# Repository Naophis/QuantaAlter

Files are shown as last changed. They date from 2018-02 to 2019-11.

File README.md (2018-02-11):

# Quanta Alter

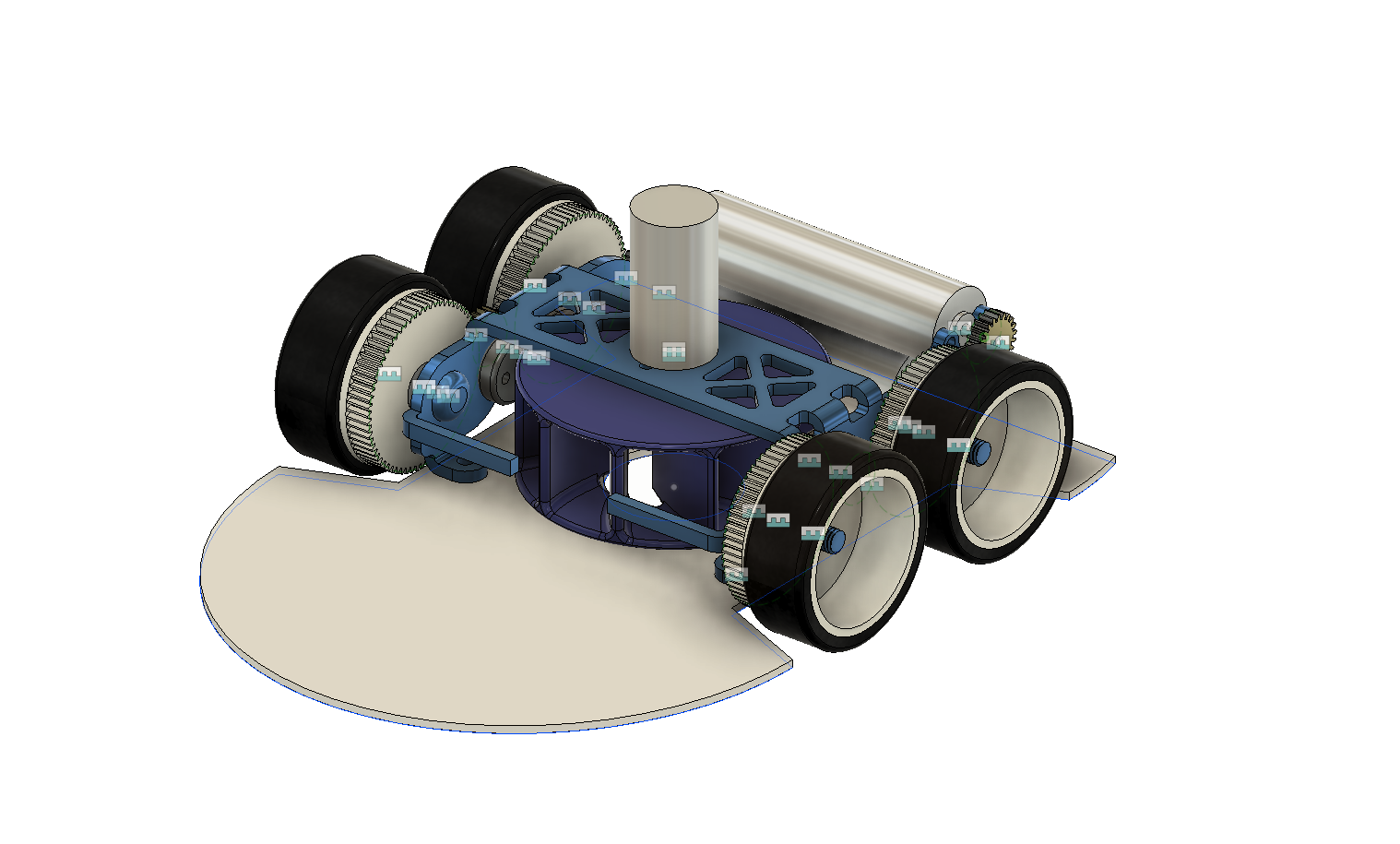
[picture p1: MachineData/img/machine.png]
QuantaAlter


## Getting started
```
git clone https://github.com/Naophis/QuantaAlter.git
```
## IDE
* e2studio

## Editor
* Visual Studio Code

## Writer
* Renesas Flash Programmer
  * Baudrate: 1228800 [bps]

## Machine Info
| | | |
|:---|---:|:---:|
|CPU|RX71M| - |
|Xtal|24M| - |
|Battery|3Cell| Lipo(4.2*3) |

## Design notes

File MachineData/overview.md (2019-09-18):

# ExiaAlter

| ||
|---|---|
|RobotName| ExiaAlter|
|Designer| Naoto Hiramatsu|
|Dimension | Width: 76.0mm, Length: 99.0mm, Height: 40.0mm|
|Weight| 110.0g |
|MCU|Renesas: R5F571MFCDFP|
|Mortor|Drive DCX-10L×2, Suction DCX-10S|
|Mortor Driver|TB6614FNG|
|Wall Sensor|SFH4550×5, ST-1KL3A×5|
|Gyroscope|ICM-20689|
|Battery|Lipo: Hyperion G5 200mah×3 3S(11.1V)|
|Gear ratio|21:67(M0.3)|
|TireSize|Diameter: 24.0m, Width: 8.5mm|
|Top/Turn Velocity|5.3m/s, 1.5~2.4m/s|

Features
* Suction is used both maze run and fast run.
* "ExiaConsole", which is Original Adjustment System, make adjustment time to be short. This console which is written in JavaSctipt can adjust almost all parameter on Web Browser and send/recieve data with UART. Robots recieve data from Console, write on Flash and use in running.

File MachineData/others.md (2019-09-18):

# Others

|	No	|	Name	|	Maker	|	Amount	|	Link	|	Remarks	|
|	---	|	---	|	---	|	---	|	---	|	---	|
|	1	| DCX10L(4.5orm) with easy10-encoder	| MAXON		|	2	|[URL](https://www.maxonjapan.co.jp/maxon/view/product/motor/dcmotor/DCX/DCX10/DCX10S01EBKL550)|	for driver	|
|	2	|	 DCX10S(3.orm)	|MAXON|	1	| [URL](https://www.maxonjapan.co.jp/maxon/view/product/motor/dcmotor/DCX/DCX10/DCX10S01EBKL550)|	for suction 	|
|	3	|	suction fun 	|	DMM3D print service	|	2	|| order made	|
|	4	|	G5 200mah	|	hyperion	|	3	| [URL](https://hyperion-world.com/en/charger-battery/batteries/hyperion-g5-lipo/g5-50cmax-1s-200mah-4-2v-max-lipo-w-phr-2p-connector)|	LiPo Battery	|
|	5	|	motor mount (frame)	|	NPS 	|	1	|| order made	|
|	6	|	zig	|	DMM3D 	|	2	|| order made	|
|	7	|	M0.3-67T-3mm-8mm(POM)	|	misumi 	|	4	|| Spur Gear	|
|	8	| M-0.3-21T-2mm-1.5mm(BRASS)	|	kkpmo 	|	4	|[URL](https://shop.kkpmo.com)| pinion	|

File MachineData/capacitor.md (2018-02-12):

# Capacitor

|	No	|	Value	|	Size	|	Amount	|	Link	|	Remarks	|
|	---	|	---	|	---	|	---	|	---	|	---	|
|	1	|	0.1u	|		|	10	|[URL](	https://www.digikey.jp/product-detail/ja/murata-electronics-north-america/GRM155R71C104JA88D/490-6327-1-ND/3845524	)|		|
|	2	|	180uF	|		|	2	|[URL](	https://www.sengoku.co.jp/mod/sgk_cart/detail.php?code=EEHD-4J4A	)|	motoro driver 	|
|	3	|	180uF	|		|	2	|[URL](	https://www.digikey.jp/product-detail/ja/wurth-electronics-inc/870235373002/732-6342-1-ND/5147893	)|	↑ or this	|
|	4	|	22u	|		|	1	|[URL](	https://www.digikey.jp/product-detail/ja/taiyo-yuden/TMK316BBJ226ML-T/587-3246-1-ND/3660105	)|	DCDC output	|
|	5	|	10u	|		|	1	|[URL](	https://www.digikey.jp/product-detail/ja/murata-electronics-north-america/GRM319R61E106KA12D/490-5525-1-ND/2334921	)|	DCDC input	|
|	6	|	1u	|		|	1	|[URL](	https://www.digikey.jp/product-detail/ja/kemet/C1206C105K4RACTU/399-1254-1-ND/411529	)|	LDO Output	|
|	7	|	10n	|		|	1	|[URL](	https://www.digikey.jp/product-detail/ja/murata-electronics-north-america/GRM155R71H103KA88D/490-4516-1-ND/1033275	)|	gyro	|
|	8	|	0.47u	|		|	1	|[URL](	https://www.digikey.jp/product-detail/ja/taiyo-yuden/JMK105BJ474KV-F/587-1230-1-ND/931007	)|	gyro	|
|	9	|	2.2u	|		|	1	|[URL](	https://www.digikey.jp/product-detail/ja/murata-electronics-north-america/GRM155R60J225ME15D/490-4519-1-ND/1033278	)|	gyro	|
|	10	|	8p	|		|	2	|[URL](	https://www.digikey.jp/product-detail/ja/murata-electronics-north-america/GRM1555C1E8R0CA01D/490-11372-1-ND/5333212	)|	xtal	|

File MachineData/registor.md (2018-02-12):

# register

|	No	|	Value	|	Size[mm]	|	Amount	|	Link	|	Remarks	|
|	---	|	---	|	---	|	---	|	---	|	---	|
|	1	|	1k	|	1005	|	12	|[URL](	https://www.digikey.jp/product-detail/ja/susumu/RG1005P-102-B-T5/RG10P1.0KBCT-ND/968960	)|		|
|	2	|	10k	|	1005	|	12	|[URL](	https://www.digikey.jp/product-detail/ja/susumu/RG1005P-103-B-T5/RG10P10KBCT-ND/968984	)|	for pull up	|
|	3	|	133	|	3126	|	1	|[URL](	https://www.digikey.jp/product-detail/ja/stackpole-electronics-inc/RMCF1206FT133R/RMCF1206FT133RCT-ND/5049846	)|	for dcdc 	|
|	4	|	3k	|	1005	|	10	|[URL](	https://www.digikey.jp/product-detail/ja/susumu/RR0510P-302-D/RR05P3.0KDCT-ND/432947	)|	for battery register	|
|	5	|	18	|	3216	|	5	|[URL](	https://www.digikey.jp/product-detail/ja/susumu/HRG3216Q-18R0-D-T1/408-1889-1-ND/5762672	)|	for sensor led	|
|	6	|	50	|	1608	|	5	|[URL](	https://www.digikey.jp/product-detail/ja/rohm-semiconductor/ESR03EZPJ510/RHM51DCT-ND/4053797	)|	for buzzer	|

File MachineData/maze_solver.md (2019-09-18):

# maeze solver(adachi method)

## introduce 
* maze size =16*16
```
uint8 maze[16][16];  // input wall exist data and came data.
uint8 dist[16][16];  // input distance for goal
```

## Adachi method 

`Adachi Method` is specialized for micromouse as maze solver.
It is based on DFS algorithm.

this document explain about this method.

this method made up of 6step.

### overview 

```
search start 
 loop 
   0. if you reached goal break.
   1. get sensor data
   2. input matrix for distance map
   3. update distance map
   4. select next cell
   5. move your mouse selected cell
   next loop
```

## Step1 (getting data)

Getting sensor data with A/D converter,
and detect exist wall.

```cpp
// sensor.left is sensor raw data getting by A/D convertor.
bool exist_left_side_wall = sensor.left > sensor_threathold.left;

// input data 
input_wall_data(uint8 x,uint8 y,uint8 direction, bool exist);
```

## Steo2 (input data in matrix)

```cpp
/**
 *  input wall data 
 *  @param x: update cell of x
 *  @param x: update cell of y
 *  @param direction  :update cell of direction
 *  @param exist : true / false(not exist)
 *  // data format is 0xff
 *  //                   S W E N | S W E N  <- this character means write below.
 *  //                   0 0 0 0 | 0 0 0 0
 *  // <-4bit is confirmed  flag |  4bit is wall exist flag ->
 *  // N : North = 0x01
 *  // E : East  = 0x02
 *  // W : West  = 0x04
 *  // S :South  = 0x08
 * 
 *  // ex) input input_wall_data(3,1,North,true)
 *  // you should this data convert to below
 *  // map[3][1] |= 0x11;
 */

void input_wall_data(uint8 x,uint8 y,uint8 direction, bool exist){

	if (x < 0 || x >= MAZE_SIZE || y < 0 || y >= MAZE_SIZE) {
		return;
	}
	map[x][y] |= (0x10 * dir); // if you input 8(south), 0x80
	if (isWall) {
		map[x][y] |= 0x01 * dir;
	} else {
		map[x][y] = (map[x][y] & 0xf0) | (map[x][y] & (~(0x01 * dir) & 0x0f));
	}
}
```

## step3 (update distance map)

`distance map` is `matrix data of distance information to goal`.  
It is based on DFS, Goal distance is 0.
So, your robots should follow to this distance number to be lower.

```cpp
//reflesh
for(uint8 i=0;i<16;i++){
    for(uint8 j=0;j<16;j++){
        dist[i][j]=255; //255 = max value of 16*16 size maze.
    }
}

// goal cell to be 0.
dist[7][7]=0; // ex) (7,7) is goal.

// update this search algo O(n^3) too heavy.
// but there is more faster algo
for(uint8 d=0;d<255;d++){
    bool update = false;
    for(uint8 i=0;i<16;i++){
        for(uint8 j=0;j<16;j++){
            tmp_dist = dist[i][j];
            if (tmp_dit == d){
                // if (i,j)'s north wall is not exist (i,j+1)'s dist = (i,j)+1
                
                // if (i,j)'s east wall is not exist (i+1,j)'s dist = (i,j)+1
                
                // if (i,j)'s west wall is not exist (i-1,j)'s dist = (i,j)+1
                
                // if (i,j)'s south wall is not exist (i,j-1)'s dist = (i,j)+1
                update=true;
            }
        }
    }
    if(!update){
        break; //end
    }
}

```

## step4 (select next cell)

find around your cell and select next cell.

```
your mouse is putting (2,2).
candidate cell is (2,3),(3,2),(1,2),(2,1)
but your wall matrix data on wall[2][2] is 0xf6, // "f" is proof of you came (2,2)
just mean exist East and West wall.
so your robots can select only (2,3),(2,1)
and 
if dist[2][3] is 15, dist[2][1] is 11
your robots should select (2,1) ,
so go to South!!

```

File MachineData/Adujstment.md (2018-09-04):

# 調整手順

* 直進の姿勢制御の中央値を見つける
  * 閾値を変更し、片側だけ制御させ通常直進させる。
  * わざと斜めにした状態で走行を開始
  * ３～４区画ほど走らせ、区画にの中心に収束するように中央値を修正する
  * ↑を左右それぞれ行う
* タイヤ径を確認する
  * 姿勢制御を入れた状態で、5区画(180[mm]*5)程走らせる
* 探索用前壁制御を調整する
  * 正面の壁に対して、2区画と少し離した状態で走行する
* 探索用壁切れを調整する
  * 調整する側の壁を入れて１走行する
* 最短用横壁壁切れを調整する
  * 何ミリ手前で曲がるかを決める
* 最短用前壁壁アリ制御を調整する
  * 壁切れする側の横壁を撤去し、前壁だけでもんだいなくどうさをするかを確認する

* 探索用前壁制御を調整する
  *

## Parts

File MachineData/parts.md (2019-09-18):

# IC Parts

|	No	|	Name	|	Amount	|	Link	|	Remarks	|
|	---	|	---	|	---	|	---	|	---	|
|	1	|	RX71M_100pin	|	1	|[URL](	https://jp.rs-online.com/web/p/microcontrollers/1262515/?searchTerm=Renesas+Electronics+マイコン+R5F571MLCDFP%23V0+32ビット+CISC+RXファミリ%2C+240MHz%2C+4+MB+フラッシュ&relevancy-data=636F3D3226696E3D4931384E5461786F6E6F6D794B6E6F776E41734D504E266C753D6A61266D6D3D6D61746368616C6C7061727469616C26706D3D5E5B5C707B4C7D5C707B4E647D5C707B5A737D2D2C2F255C2E5D2B2426706F3D3530353326736E3D592673743D4B4559574F52445F4D554C54495F414C5048415F4E554D455249432677633D5249474854267573743D52656E6573617320456C656374726F6E69637320E3839EE382A4E382B3E383B3205235463537314D4C43444650235630203332E38393E38383E383882043495343205258E38395E382A1E3839FE383AA2C203234304D487A2C2034204D4220E38395E383A9E38383E382B7E383A5267374613D52656E6573617320456C656374726F6E69637320E3839EE382A4E382B3E383B3205235463537314D4C434446505630203332E38393E38383E383882043495343205258E38395E382A1E3839FE383AA2C203234304D487A2C2034204D4220E38395E383A9E38383E382B7E383A526	)|	R5F571MLCDFP	|
|	2	|	TB6614FNG	|	2	|[URL](	https://www.digikey.jp/product-detail/ja/toshiba-semiconductor-and-storage/TB6614FNG,C,EL/TB6614FNGCELCT-ND/3671341	)|	Production Stopped	|
|	3	|	icm20689	|	1	|[URL](	https://www.digikey.jp/product-detail/ja/tdk-invensense/ICM-20689/1428-1059-1-ND/5872874	)|	Successor Model MPU6050	|
|	4	|	LXDC55FAAA-203	|	1	|[URL](	http://akizukidenshi.com/catalog/g/gM-09577/	)|	DCDC(Target Output is 5V)	|
|	5	|	SFH4550	|	5	|[URL](	https://www.digikey.jp/product-detail/ja/osram-opto-semiconductors-inc/SFH-4550/475-1200-ND/806365	)|  IR LED		|
|	6	|	ST-1KL3A	|	5	|[URL](	https://www.rt-shop.jp/index.php?main_page=product_info&cPath=42&products_id=2747	)| photo transistor	|
|	7	|	Xtal24MHz	|	1	|[URL](	https://www.digikey.jp/product-detail/ja/txc-corporation/7V-24.000MAAV-T/887-1805-1-ND/3585998	)|		|
|	8	|	2chNPN transister	|	3	|[URL](	https://www.digikey.jp/product-detail/ja/on-semiconductor/FDC6561AN/FDC6561ANCT-ND/965590	)|	for LED & buzzer	|
|	9	|	buzzer	|	1	|[URL](	https://www.digikey.jp/product-detail/ja/pui-audio-inc/SMT-0540-T-7-R/668-1207-1-ND/2207546	)|		|
|	10	|	diode	|	2	|[URL](	http://akizukidenshi.com/catalog/g/gI-02073/	)|	for buzzer & vacume 	|
|	11	|	LDO（3.3V)	|	1	|[URL](	https://www.marutsu.co.jp/pc/i/14264/	)|	main volt	|
|	12	|	tack switch	|	2	|[URL](	https://www.digikey.jp/product-detail/ja/omron-electronics-inc-emc-div/B3U-1000P/SW1020CT-ND/1534357	)|	for rest / mode switch	|
|	13	|	center push switch	|	1	|[URL](	https://jp.rs-online.com/web/p/joystick-switches/1239637/?searchTerm=Alps+多重制御スイッチ%2CCenter-Push%2C+4軸&relevancy-data=636F3D3226696E3D4931384E5461786F6E6F6D794B6E6F776E41734D504E266C753D6A61266D6D3D6D61746368616C6C7061727469616C26706D3D5E5B5C707B4C7D5C707B4E647D5C707B5A737D2D2C2F255C2E5D2B2426706F3D3530353326736E3D592673743D4B4559574F52445F4D554C54495F414C5048415F4E554D455249432677633D5249474854267573743D416C707320E5A49AE9878DE588B6E5BEA1E382B9E382A4E38383E383812C43656E7465722D507573682C2034E8BBB8267374613D416C707320E5A49AE9878DE588B6E5BEA1E382B9E382A4E38383E383812C43656E7465722D507573682C2034E8BBB826	)|	ui switch	|
|	14	|	Pch FET	|	1	|[URL](	https://www.digikey.jp/product-detail/ja/vishay-siliconix/SI3493BDV-T1-E3/SI3493BDV-T1-E3CT-ND/1656885	)|	vacume	|
|	15	|	Nch FET	|	1	|[URL](	https://www.digikey.jp/product-detail/ja/vishay-siliconix/SI3410DV-T1-GE3/SI3410DV-T1-GE3CT-ND/2441908	)|	led	|
|	16	|	slide switch	|	1	|[URL](	https://www.digikey.jp/product-detail/ja/c-k/PCM12SMTR/401-2016-1-ND/1640125	)|	main	|
|	17	|	pin socket	|		|[URL](	http://akizukidenshi.com/catalog/g/gC-00661/	)|	for motor	|
|	18	|	pin header	|		|[URL](	http://akizukidenshi.com/catalog/g/gC-02900/	)|	for motor	|
|	19	|	ui led 1608	|		|[URL](		)|	ui	|

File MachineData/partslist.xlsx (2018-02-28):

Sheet: IC
| | No | | | Name | | | Amount | | | Link | | | Remarks
| | --- | | | --- | | | --- | | | --- | | | ---
| | 1 | | | RX71M_100pin | | | 1 | |[URL]( | https://jp.rs-online.com/web/p/microcontrollers/1262515/ | )| | R5F571MLCDFP
| | 2 | | | TB6614FNG | | | 2 | |[URL]( | https://www.digikey.jp/product-detail/ja/toshiba-semiconductor-and-storage/TB6614FNG,C,EL/TB6614FNGCELCT-ND/3671341 | )| | Production Stopped
| | 3 | | | icm20689 | | | 1 | |[URL]( | https://www.digikey.jp/product-detail/ja/tdk-invensense/ICM-20689/1428-1059-1-ND/5872874 | )| | Successor Model MPU6050
| | 4 | | | LXDC55FAAA-203 | | | 1 | |[URL]( | http://akizukidenshi.com/catalog/g/gM-09577/ | )| | DCDC(Target Output is 5V)
| | 5 | | | SFH4550 | | | 5 | |[URL]( | https://www.digikey.jp/product-detail/ja/osram-opto-semiconductors-inc/SFH-4550/475-1200-ND/806365 | )
| | 6 | | | ST-1KL3A | | | 5 | |[URL]( | https://www.rt-shop.jp/index.php?main_page=product_info&cPath=42&products_id=2747 | )
| | 7 | | | Xtal24MHz | | | 1 | |[URL]( | https://www.digikey.jp/product-detail/ja/txc-corporation/7V-24.000MAAV-T/887-1805-1-ND/3585998 | )
| | 8 | | | 2chNPN transister | | | 3 | |[URL]( | https://www.digikey.jp/product-detail/ja/on-semiconductor/FDC6561AN/FDC6561ANCT-ND/965590 | )| | for LED & buzzer | | | https://www.digikey.jp/product-detail/ja/on-semiconductor/NDC7002N/NDC7002NCT-ND/244288
| | 9 | | | buzzer | | | 1 | |[URL]( | https://www.digikey.jp/product-detail/ja/pui-audio-inc/SMT-0540-T-7-R/668-1207-1-ND/2207546 | )
| | 10 | | | diode | | | 2 | |[URL]( | http://akizukidenshi.com/catalog/g/gI-02073/ | )| | for buzzer & vacume
| | 11 | | | LDO（3.3V) | | | 1 | |[URL]( | https://www.marutsu.co.jp/pc/i/14264/ | )| | main volt
| | 12 | | | tack switch | | | 2 | |[URL]( | https://www.digikey.jp/product-detail/ja/omron-electronics-inc-emc-div/B3U-1000P/SW1020CT-ND/1534357 | )| | for rest / mode switch
| | 13 | | | center push switch | | | 1 | |[URL]( | https://jp.rs-online.com/web/p/joystick-switches/1239637/?searchTerm=Alps+多重制御スイッチ%2CCenter-Push%2C+4軸 | )| | ui switch
| | 14 | | | Pch FET | | | 1 | |[URL]( | https://www.digikey.jp/product-detail/ja/vishay-siliconix/SI3493BDV-T1-E3/SI3493BDV-T1-E3CT-ND/1656885 | )| | vacume
| | 15 | | | Nch FET | | | 1 | |[URL]( | https://www.digikey.jp/product-detail/ja/vishay-siliconix/SI3410DV-T1-GE3/SI3410DV-T1-GE3CT-ND/2441908 | )| | led
| | 16 | | | slide switch | | | 1 | |[URL]( | https://www.digikey.jp/product-detail/ja/c-k/PCM12SMTR/401-2016-1-ND/1640125 | )| | main
| | 17 | | | pin socket | | |  | |[URL]( | http://akizukidenshi.com/catalog/g/gC-00661/ | )| | for motor
| | 18 | | | pin header | | |  | |[URL]( | http://akizukidenshi.com/catalog/g/gC-02900/ | )| | for motor
| | 19 | | | ui led 1608 | | |  | |[URL]( |  | )| | ui
 |  |  | half sensor led |  |  |  | http://akizukidenshi.com/catalog/g/gI-04313/
 |  |  | drv8838

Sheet: register
| | No | | | Value | | | Size | | | Amount | | | Link | | | Remarks
| | --- | | | --- | | | --- | | | --- | | | --- | | | ---
| | 1 | | | 1k | | | 1005 | | | 12 | |[URL]( | https://www.digikey.jp/product-detail/ja/susumu/RG1005P-102-B-T5/RG10P1.0KBCT-ND/968960 | )
| | 2 | | | 10k | | | 1005 | | | 12 | |[URL]( | https://www.digikey.jp/product-detail/ja/susumu/RG1005P-103-B-T5/RG10P10KBCT-ND/968984 | )| | for pull up
| | 3 | | | 133 | | | 3126 | | | 1 | |[URL]( | https://www.digikey.jp/product-detail/ja/stackpole-electronics-inc/RMCF1206FT133R/RMCF1206FT133RCT-ND/5049846 | )| | for dcdc
| | 4 | | | 3k | | | 1005 | | | 10 | |[URL]( | https://www.digikey.jp/product-detail/ja/susumu/RR0510P-302-D/RR05P3.0KDCT-ND/432947 | )| | for battery register
| | 5 | | | 18 | | | 3216 | | | 5 | |[URL]( | https://www.digikey.jp/product-detail/ja/susumu/HRG3216Q-18R0-D-T1/408-1889-1-ND/5762672 | )| | for sensor led
| | 6 | | | 50 | | | 1608 | | | 5 | |[URL]( | https://www.digikey.jp/product-detail/ja/rohm-semiconductor/ESR03EZPJ510/RHM51DCT-ND/4053797 | )| | for buzzer

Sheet: capacitor
| | No | | | Value | | | Size | | | Amount | | | Link | | | Remarks
| | --- | | | --- | | | --- | | | --- | | | --- | | | ---
| | 1 | | | 0.1u | | | 1005 | | | 10 | |[URL]( | https://www.digikey.jp/product-detail/ja/murata-electronics-north-america/GRM155R71C104JA88D/490-6327-1-ND/3845524 | )
| | 2 | | | 180uF | | |  | | | 2 | |[URL]( | https://www.sengoku.co.jp/mod/sgk_cart/detail.php?code=EEHD-4J4A | )| | motoro driver
| | 3 | | | 180uF | | |  | | | 2 | |[URL]( | https://www.digikey.jp/product-detail/ja/wurth-electronics-inc/870235373002/732-6342-1-ND/5147893 | )| | ↑ or this
| | 4 | | | 22u | | | 3216 | | | 1 | |[URL]( | https://www.digikey.jp/product-detail/ja/taiyo-yuden/TMK316BBJ226ML-T/587-3246-1-ND/3660105 | )| | DCDC output
| | 5 | | | 10u | | | 3216 | | | 1 | |[URL]( | https://www.digikey.jp/product-detail/ja/murata-electronics-north-america/GRM319R61E106KA12D/490-5525-1-ND/2334921 | )| | DCDC input
| | 6 | | | 1u | | | 3216 | | | 1 | |[URL]( | https://www.digikey.jp/product-detail/ja/kemet/C1206C105K4RACTU/399-1254-1-ND/411529 | )| | LDO Output
| | 7 | | | 10n | | | 1005 | | | 1 | |[URL]( | https://www.digikey.jp/product-detail/ja/murata-electronics-north-america/GRM155R71H103KA88D/490-4516-1-ND/1033275 | )| | gyro
| | 8 | | | 0.47u | | | 1005 | | | 1 | |[URL]( | https://www.digikey.jp/product-detail/ja/taiyo-yuden/JMK105BJ474KV-F/587-1230-1-ND/931007 | )| | gyro
| | 9 | | | 2.2u | | | 1005 | | | 1 | |[URL]( | https://www.digikey.jp/product-detail/ja/murata-electronics-north-america/GRM155R60J225ME15D/490-4519-1-ND/1033278 | )| | gyro
| | 10 | | | 8p | | | 1005 | | | 2 | |[URL]( | https://www.digikey.jp/product-detail/ja/murata-electronics-north-america/GRM1555C1E8R0CA01D/490-11372-1-ND/5333212 | )| | xtal

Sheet: radicon
| | No | | | Name | | | Amount | | | Link | | | Remarks
| | --- | | | --- | | | --- | | | --- | | | ---
| | 1 | | | DDL630zz | | | 8 | |[URL]( | http://www.dendouki.com/fs/dendouki/gr3179/nmb-ddl-630zz | )
| | 2 | | | DDLF520zz | | | 4 | |[URL]( | http://www.dendouki.com/fs/dendouki/gr3214/nmb-ddlf-520zz | )
| | 3 | | | 平行ピン8mm | | | 2 | |[URL]( | https://www.monotaro.com/p/4215/5766/?t.q=%95%BD%8Ds%83s%83%93 | )
| | 4 | | | ピニオン M03_21_Φ2.0_2T | | | 2 | |[URL]( | https://shop.kkpmo.com/product_info.php?info=p383_gearwheel-pinion-m0-3---21teeth.html | )
| | 5 | | | ピニオン M03_21_Φ1.5_2T | | | 2 | |[URL]( | https://shop.kkpmo.com/product_info.php?info=p383_gearwheel-pinion-m0-3---21teeth.html | )
| | 6 | | | スパーギア M03_67_Φ8_3T | | | 4 | |[URL]( | http://cp.misumi.jp/misumicp/itemDetail.html?itemId=HP30001 | )| | GEBA-JW-A0.3-G67-P8-B3
| | 7 | | | ネジM1.4_5.5mm | | | 4 | |[URL]( | http://wilco.jp/products/F/F-N-03.html | )
| | 8 | | | ナットM1.4 | | | 4 | |[URL]( | http://wilco.jp/products/U/UNTD.html | )
| | 9 | | | MZH131W-N25 | | | 4 | |[URL]( | http://rc.kyosho.com/ja/mzh131w-n25.html | )
| | 10 | | | タイヤ_ローハイト | | | 4 | |[URL]( | https://www.rt-shop.jp/index.php?main_page=product_info&cPath=1002_1024_1033&products_id=3600 | )
| | 11 | | | タイヤ_ノーマル | | |  | |[URL]( | https://www.rt-shop.jp/index.php?main_page=product_info&cPath=1348_18&products_id=1249 | )

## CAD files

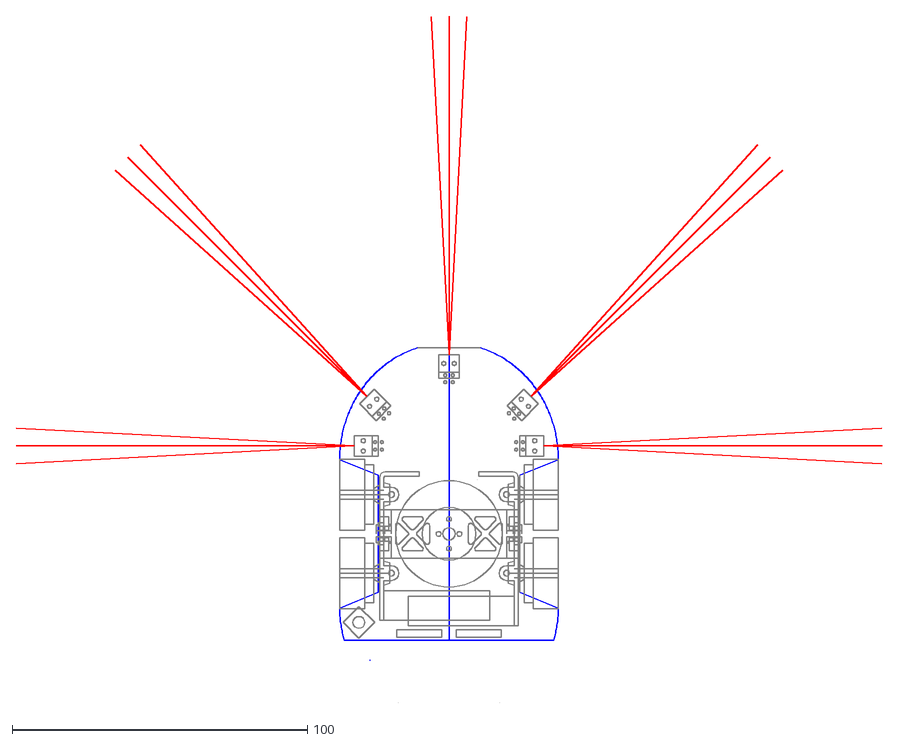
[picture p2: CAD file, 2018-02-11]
MachineData/cad/QuantaAlter.DXF
293.1 x 232.4

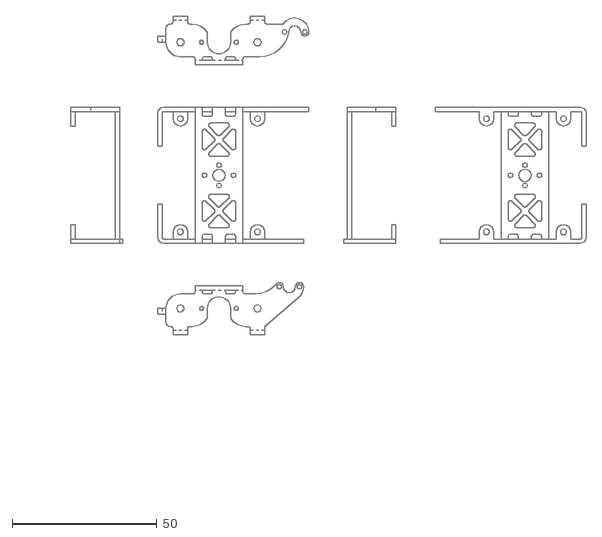
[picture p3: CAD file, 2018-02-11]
MachineData/cad/MotorMount.DXF
196.6 x 165.8

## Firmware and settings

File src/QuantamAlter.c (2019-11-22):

#include "iodefine.h"
#include "stdio.h"
#include <stdint.h>
#include <string.h>
#include "machine.h"
#include "mathf.h"
#include "config/defines.h"
#include "config/Table.h"

#include "config/Structor.h"

#include "config/init.h"
#include "serial.h"
#include "spi.h"
#include "Music.h"

#include "config/ParamDef.h"
#include "sensor.h"

#include "config/ParamDef.h"
#include "config/ParamsController.h"
#include "config/ParamUartImporter.h"
#include "Util.h"
#include "PhysicalBasement.h"

#include "motion/Run.h"
#include "motion/DistCalc.h"
#include "motion/WallOff.h"
//#include "motion/WallOff2.h"
#include "search/Map.h"
#include "search/Search.h"
#include "search/VectorSearch.h"
#include "search/VectorPath.h"
#include "Path.h"
#include "motion/RealRun.h"

#include "flash/r_flash_rx_config.h"
#include "flash/r_flash_rx_if.h"
#include "flash/flash.h"

#include "search/Adachi.h"
#include "search/cirkit.h"

//#include "config/ParamImporter.h"

#include "config/Setting.h"
//#include "Mram.h"
#include "Action.h"
#include "OperationSystem.h"
#include "config/SerialMapper.h"

volatile void buzzer() {
	buzzerTimer++;
	if (m_time > 0 && buzzerTimer >= m_time) {
		stopCmt1();
	}
}
volatile void mtu6A() {
	PORTD.PODR.BIT.B7 = 1;
}
volatile void mtu6B() {
	PORTD.PODR.BIT.B7 = 0;
}
volatile char rightTrend = 0;
volatile char leftTrend = 0;
volatile signed short gyros[4];

volatile void cmt() {
	timer++;
	time++;
	if (singing) {
		buzzerTimer++;
		if (m_time > 0 && buzzerTimer >= (CMT_CYCLE / 1000) * m_time) {
			stopCmt1();
		}
	}
	sinCount++;
	swTop = !PushTop;
	swBottom = !PushBottom;
	swRight = !PushRight;
	swLeft = !PushLeft;
	swCenter = !PushCenter;
	if (!singing) {
		if (!PushTop) {
			cmtMusic(C2_, 100);
		}
		if (!PushRight) {
			cmtMusic(D2_, 100);
		}
		if (!PushLeft) {
			cmtMusic(E2_, 100);
		}
		if (!PushBottom) {
			cmtMusic(F2_, 100);
		}
	}
	Physical_Basement();
	if ((logs < (L_Length - 1)) && (cc == 1) && (time >= 0)) {
		if ((time % (char) (logterm)) == 0) {
			log1[logs] = (int) (V_now);
			log3[logs] = (V_Enc.r + V_Enc.l) / 2;
			log4[logs] = (ang * 180 / PI); //ジャイロ
			log5[logs] = Duty_l * 100;
			log6[logs] = Duty_r * 100;
			log7[logs] = (battery);
			log8[logs] = (LS_SEN45.now);
			log9[logs] = (RS_SEN45.now);
			logs10[logs] = Se.error_now;
			log11[logs] = (Front_SEN.now);
			log12[logs] = (settleGyro);
			log13[logs] = (W_now);
			log14[logs] = (angle * 180 / PI); //理論値
			log15[logs] = V_Enc.r;
			log16[logs] = V_Enc.l;
			log17[logs] = (float) (alpha);
			log18[logs] = px2; //lastPeekR;
			log19[logs] = (feadforward_para(L));
			log20[logs] = (feadforward_para(R));
			log21[logs] = (LS_SEN2.now);
			log22[logs] = (RS_SEN2.now);
			float tmpRightRef = sen_r_dia_img[(int) img_dist_r];
			float tmpRightRef90 = sen_r90_dia[(int) img_dist_r];
			float tmpLeftRef = sen_l_dia_img[(int) img_dist_l];
			float tmpLeftRef90 = sen_l90_dia[(int) img_dist_l];

			log23[logs] = sen_l2[0];
			log24[logs] = sen_r2[0];

			log25[logs] = C.g;
			log26[logs] = C.s;
			log27[logs] = C.v;
			log28[logs] = globalState;
			log29[logs] = Se2.error_now;

			log30[logs] = tmpLeftRef;
			log31[logs] = tmpLeftRef90;

			log32[logs] = distance;
			log33[logs] = img_distance;
			log34[logs] = C.angles;
			log35[logs] = img_dist_l;
			log36[logs] = img_dist_r;

			logs++;
		}
	}

	if (enableSystemIdentification && timer < DETECT_SYS_ID_Length) {
		vrlist[timer] = V_Enc.r;
		vllist[timer] = V_Enc.l;
		gyrolist[timer] = settleGyro;
		dutylist[timer] = (*(float *) 1049472) / battery * M_CYCLE;
	}

}

volatile int timer2 = 0;

void mtu4_A() {
	tpu_count++;
	switch (tpu_count) {
	case 1:
		timer2++;
		if (mpu) {
			callMpu(0x47);
		}
		PORTD.PODR.BIT.B6 = 1; //Front
		break;
	case 2:
		if (mpu) {
			callMpu(0x47);
		}
		PORTE.PODR.BIT.B0 = 1; //Right45
		PORT2.PODR.BIT.B5 = 1; //Left45
		break;
	case 3:
		if (mpu) {
			callMpu(0x47);
		}
		PORTE.PODR.BIT.B1 = 1; //Right90
		PORT2.PODR.BIT.B4 = 1; //Left90
		break;
	case 4:
		if (fanStart) {
			const float minVoltage = *(float *)1049852;
			float tmpBattery = max(battery, minVoltage);

			if (fanMode == TestRun) {
				GPT2.GTCCRA = (short) (myVacumeDuty / tmpBattery * FAN_CYCLE);
				GPT2.GTCCRC = (short) (myVacumeDuty / tmpBattery * FAN_CYCLE);
			} else if (fanMode == FastRun) {
				GPT2.GTCCRA = (short) (FAN_AMP / tmpBattery * FAN_CYCLE);
				GPT2.GTCCRC = (short) (FAN_AMP / tmpBattery * FAN_CYCLE);
			} else if (fanMode == FastRun2) {
				GPT2.GTCCRA = (short) (fastRunFanV2 / tmpBattery * FAN_CYCLE);
				GPT2.GTCCRC = (short) (fastRunFanV2 / tmpBattery * FAN_CYCLE);
			} else if (fanMode == SearchRun) {
				GPT2.GTCCRA = (short) (FAN_AMP2 / tmpBattery * FAN_CYCLE);
				GPT2.GTCCRC = (short) (FAN_AMP2 / tmpBattery * FAN_CYCLE);
			} else if (fanMode == CtrlFan) {
				GPT2.GTCCRA = (short) (FAN_AMP3 / tmpBattery * FAN_CYCLE);
				GPT2.GTCCRC = (short) (FAN_AMP3 / tmpBattery * FAN_CYCLE);
			} else if (fanMode == CtrlFan2) {
				GPT2.GTCCRA = (short) (FAN_AMP4 / tmpBattery * FAN_CYCLE);
				GPT2.GTCCRC = (short) (FAN_AMP4 / tmpBattery * FAN_CYCLE);
			} else if (fanMode == CtrlFan3) {
				GPT2.GTCCRA = (short) (FAN_AMP5 / tmpBattery * FAN_CYCLE);
				GPT2.GTCCRC = (short) (FAN_AMP5 / tmpBattery * FAN_CYCLE);
			}else if (fanMode == CtrlFan4) {
				GPT2.GTCCRA = (short) (FAN_AMP6 / tmpBattery * FAN_CYCLE);
				GPT2.GTCCRC = (short) (FAN_AMP6 / tmpBattery * FAN_CYCLE);
			}
		} else {
			GPT2.GTCCRA = GPT2.GTCCRC = 0;
		}
		if (mpu) {
			callMpu(0x47);
		}
		break;
	}
}

void getBattery() {
	float tmp = 3.34;
	if (BATTERY != 0) {
		battery = 0.1 * tmp * BATTERY / 4096 * 4 + 0.9 * batteryOld;
	} else {
		battery = tmp * BATTERY / 4096 * 4;
	}
	batteryOld = battery;
}
void mtu4_B() {
	switch (tpu_count) {
	case 1:
		sensing_front();
		gyros[0] = (signed short) getMpuData();
		break;
	case 2:
		sensing_side();
		gyros[1] = (signed short) getMpuData();
		break;
	case 3:
		sensing_side2();
		gyros[2] = (signed short) getMpuData();
		break;
	case 4:
		sensing_in_off();
		gyros[3] = (signed short) getMpuData();

		RS_SEN45.old = RS_SEN45.now;
		LS_SEN45.old = LS_SEN45.now;
		Front_SEN.old = Front_SEN.now;
		RS_SEN2.old = RS_SEN2.now;
		LS_SEN2.old = LS_SEN2.now;

		getSensorData();
		float tmpGyros = 0.250 * (gyros[0] + gyros[1] + gyros[2] + gyros[3]);
		// float tmpGyros = gyros[3];
//		float tmpGyros = 0.50 * (gyros[0] + gyros[2]);

		settleGyro2 = (tmpGyros - G.ref) * G.th;

		float diffOder = *(float *) 1049748;
		char gyroMode = (char) (*(float *) 1049752);
		float gyrooffset = *(float *) 1049756;

		if ((W_now - settleGyro2) > diffOder
				|| (settleGyro2 - W_now) > diffOder) {
			settleGyro = W_now + gyrooffset;
			settleGyroOld = settleGyro;
			G.now = settleGyro;
			G.old = settleGyro;
		} else {
			G.now = settleGyro2;
			settleGyroOld = settleGyro;
			if (gyroMode == true) {
				settleGyro = 0.1 * G.now + 0.9 * G.old;
			} else {
				settleGyro = G.now;
			}
			char gyroConfig2 = (char) (*(float *) 1049820);
			if (gyroConfig2) {
				G.old = settleGyro2;
			} else {
				G.old = settleGyro;
			}
		}

		tpu_count = 0;

		for (char i = 4; i > 0; i--) {
			// sen_log_r[i] = sen_log_r[i - 1];
			// sen_log_l[i] = sen_log_l[i - 1];
			// sen_log_front[i] = sen_log_front[i - 1];
			// sen_r[i] = sen_r[i - 1];
			// sen_l[i] = sen_l[i - 1];
			sen_r2[i] = sen_r2[i - 1];
			sen_l2[i] = sen_l2[i - 1];
		}
		// sen_log_r[0] = RS_SEN45.now;
		// sen_log_l[0] = LS_SEN45.now;
		// sen_r[0] = RS_SEN45.now > running_wall_off_r;
		// sen_l[0] = LS_SEN45.now > running_wall_off_l;
		sen_r2[0] = RS_SEN2.now > search_wall_off_r;
		sen_l2[0] = LS_SEN2.now > search_wall_off_l;
		// sen_log_front[0] = Front_SEN.now;
		break;
	}
	sensor_led_off();
}

void initRX64M() {
	initClock();
	initLED();
	initSensorLED();
	initMotorDriverRotate();
	initS12AD();
	initSci1();
	initCmt0();
	initIsouKeisu();
	initGPT01();
//	initGPT2();
	Init_SPI();
	init_Mtu4();
	init_Mtu6();
	myprintf("Flash Open %d\r\n", R_FLASH_Open());
	importParam();

}
void test() {
	ComFlag = true;
}

void printErrorEnum() {
	myprintf("%s %d\r\n", STR(FLASH_SUCCESS), FLASH_SUCCESS);
	myprintf("%s %d\r\n", STR(FLASH_ERR_BUSY), FLASH_ERR_BUSY);
	myprintf("%s %d\r\n", STR(FLASH_ERR_ACCESSW), FLASH_ERR_ACCESSW);
	myprintf("%s %d\r\n", STR(FLASH_ERR_FAILURE), FLASH_ERR_FAILURE);
	myprintf("%s %d\r\n", STR(FLASH_ERR_CMD_LOCKED), FLASH_ERR_CMD_LOCKED);
	myprintf("%s %d\r\n", STR(FLASH_ERR_LOCKBIT_SET), FLASH_ERR_LOCKBIT_SET);
	myprintf("%s %d\r\n", STR(FLASH_ERR_FREQUENCY), FLASH_ERR_FREQUENCY);
	myprintf("%s %d\r\n", STR(FLASH_ERR_ALIGNED), FLASH_ERR_ALIGNED);
	myprintf("%s %d\r\n", STR(FLASH_ERR_BOUNDARY), FLASH_ERR_BOUNDARY);
	myprintf("%s %d\r\n", STR(FLASH_ERR_OVERFLOW), FLASH_ERR_OVERFLOW);
	myprintf("%s %d\r\n", STR(FLASH_ERR_BYTES), FLASH_ERR_BYTES);
	myprintf("%s %d\r\n", STR(FLASH_ERR_ADDRESS), FLASH_ERR_ADDRESS);
	myprintf("%s %d\r\n", STR(FLASH_ERR_BLOCKS), FLASH_ERR_BLOCKS);
	myprintf("%s %d\r\n", STR(FLASH_ERR_PARAM), FLASH_ERR_PARAM);
	myprintf("%s %d\r\n", STR(FLASH_ERR_NULL_PTR), FLASH_ERR_NULL_PTR);
	myprintf("%s %d\r\n", STR(FLASH_ERR_UNSUPPORTED), FLASH_ERR_UNSUPPORTED);
	myprintf("%s %d\r\n", STR(FLASH_ERR_SECURITY), FLASH_ERR_SECURITY);
	myprintf("%s %d\r\n", STR(FLASH_ERR_TIMEOUT), FLASH_ERR_TIMEOUT);
}

void main(void) {
	initRX64M();
	batteryCheck();
	setupCmt = enableMPU = os_escape = true;

	while (1) {
		float result = getZeroPoint();
		if (ABS(result) < 0.01) {
			decide2(125);
			setupMpu6500();
		} else {
			break;
		}
	}
	coin(100);
	ledOn = 1;
	os_escape = 1;
	// myprintf("%c[33m", ESC); /* 文字を黄色に */
	operation();
	os_escape = 0;
}

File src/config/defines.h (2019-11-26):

/*
 * defines.h
 *
 *  Created on: 2017/07/30
 *      Author: Naoto
 */

#ifndef DEFINES_H_
#define DEFINES_H_

#define STR(var) #var   //引数にした変数を変数名を示す文字列リテラルとして返すマクロ関数

#define true 1
#define false 0
volatile char setupCmt = false;
volatile int tpu_count = 0;
#define M_CYCLE 450
#define FAN_CYCLE 450

#define FRONT_AD S12AD.ADDR3 //front P43
#define RS2 S12AD.ADDR5	 //P45
#define RS45 S12AD.ADDR4 //P44
#define LS45 S12AD.ADDR1 //P41
#define LS2 S12AD.ADDR2	//P42

#define LF S12AD.ADDR6	//P46
#define BATTERY S12AD.ADDR7	//P47

#define LED1 PORTA.PODR.BIT.B7
#define LED2 PORTB.PODR.BIT.B5
#define LED3 PORTB.PODR.BIT.B6
#define LED4 PORTB.PODR.BIT.B7
#define LED_RIGHT PORTE.PODR.BIT.B2
#define LED_LEFT PORT2.PODR.BIT.B3

volatile double settleGyro2, settleGyroOld, settleGyro;

volatile char adEnable = 1;

volatile char enableMPU = false;
float battery, batteryOld;
char fanStart = false;
char fanStart2 = false;
//#define FAN_AMP2 10.50
//#define FAN_AMP 10.50

float FAN_AMP = 9.0f;	//11.35
float FAN_AMP2 = 6.5f;	//5.0
float FAN_AMP3 = 0.0f;	//5.0
float FAN_AMP4 = 4.0f;	//5.0
float FAN_AMP5 = 3.0f;	//5.0
float FAN_AMP6 = 3.0f;	//5.0
float fastRunFanV2 = 3.0f;	//5.0

volatile float myVacumeDuty = 6.5;
//#define FAN_AMP 11.0	//11.35
const float PI = 3.141592653589793;

char TRANSAM = false;
double dt = 0.001 / 4;
#define ABS(IN) ((IN) < 0 ? - (IN) : (IN))
#define Vo 0.0f				//初速度
#define Wo 0.5f			//初期角速度
#define W_max 25.0f
//#define W_max 5.5f
volatile double W_now = 0;
volatile double alpha = 0.0;			//	[rad/s^2]
volatile double ang = 0.0;				//角度 rad
volatile double distance = 0.0;		//距離 mm
volatile double img_distance = 0.0;		//距離 mm
volatile double img_dist_r = 0.0;		//距離 mm
volatile double img_dist_l = 0.0;		//距離 mm
volatile char diaStrwallCount_r = 0;
volatile char diaStrwallCount_l = 0;
#define North 1
#define East 2
#define West 4
#define South 8
#define NorthEast 3
#define SouthEast 5
#define NorthWest 6
#define SouthWest 7
#define true 1
#define false 0

#define R 1					//探索時ターン　右フラグ
#define L 2					//探索時ターン　左フラグ
#define ROOT2 1.41421356f
#define pathLength 512

volatile float V_r = 0;
volatile float V_l = 0;
volatile float V_max = 600.0;	//最高速度
volatile float acc = 4000;		//加速度
volatile float V_now = Vo;		//現在速度
volatile float V_old = 0;
volatile float W_old = 0;
volatile unsigned short x = 0, y = 0;		//座標保持変数
volatile unsigned char path_s[pathLength];	//直進パス
volatile unsigned char path_t[pathLength];	//ターンパス

volatile unsigned int Value = 255;	//最小の評価値
volatile unsigned char next_move = North;
volatile unsigned char next_dir = North;
volatile unsigned char now_dir = North;

volatile char stop = 0;
volatile float v_sla[8];

volatile char os_escape;
volatile char fail = 0;
volatile unsigned int sinCount = 0;
volatile unsigned char sw;
volatile unsigned int time = 0;
volatile short gyro_temp[5];
volatile float gyro = 0;
volatile float tempGyro = 0;
volatile int temp_max = 0, temp_min = 5000;
volatile float oldGyroData = 0;
volatile float settlegyroData = 0;
volatile int tempGyro2 = 0;
volatile float settleGyro3 = 0;
volatile float controlSensour = 0;
volatile float controlGyro = 0;
volatile float w_r, w_l;
volatile float w_now;
volatile char positionControlValueFlg;
volatile char gyroKeepZero;
volatile char dia = 0;
volatile char frontwall_ctrl=0;
volatile float Duty_r, Duty_l;
volatile unsigned long gra_r, gra_l;

volatile unsigned int meloTimer = 0;
volatile int DutyR, DutyL;
volatile float rpmR = 0, rpmL = 0;
volatile float rpmR_old = 0, rpmL_old = 0;

volatile float logterm = 5;
volatile float isouratio = 0;
volatile float isouzure = 0;
volatile float searchrange = 0;
volatile float angle = 0;
volatile char gyroErrResetEnable = false;
volatile unsigned int cc = 0;
volatile unsigned int logs = 0;
volatile float ffR, ffL;
volatile float angle_enc;
volatile char slaFLG = 0;
volatile char gyroOn = 0;
volatile float W_now2 = 0;
volatile int EtCheck = 0;
volatile int ledOn = 0;
volatile int logData = 0;
volatile char cirquitMode = 0;
#define NAPIER 0.7632146182405746f
#define NAPIER2 0.6034501613134686f
volatile char goalChangeFlg = 0;
volatile char modeFlg = 0;
volatile char allow = 1;
volatile char weightMode = 1;
volatile char wallCut_R = 0;
volatile char wallCut_L = 0;
volatile char mode_FF = 0;
volatile char fastMode = 0;
volatile float slalomBackDistance = 0;
volatile char pathMode = 1;
volatile float tempVmax = 0;
volatile char alphaMode = 0;
volatile float alphaTemp = 0;
volatile float omegaTemp = 0;
volatile float slaTerm = 0;
volatile char runFlg = 0;
volatile char errorFlg = 0;
volatile char globalError = 0;

volatile char frontWallCtrl = 0;

volatile char isKnown = 0;

volatile float tmpData = 0;
#define MAZE_SIZE  16
volatile char dist[MAZE_SIZE][MAZE_SIZE];
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

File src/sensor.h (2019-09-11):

/*
 * sensor.h
 *
 *  Created on: 2017/07/30
 *      Author: Naoto
 */

#ifndef SENSOR_H_
#define SENSOR_H_

void sensor_led_off() {
	PORTE.PODR.BIT.B0 = 0;	//righ45
	PORTE.PODR.BIT.B1 = 0;	//right
	PORT2.PODR.BIT.B5 = 0;	//left45
	PORT2.PODR.BIT.B4 = 0;	//left
	PORTD.PODR.BIT.B6 = 0;	// fornt
}
void getBattery();
void sensing_battery() {
	S12AD.ADANSA0.BIT.ANSA0 = 0x80; //battery
	S12AD.ADCSR.BIT.ADST = 1;
	while (S12AD.ADCSR.BIT.ADST)
		;
	getBattery();
}
void sensing_in_off() {
	S12AD.ADANSA0.BIT.ANSA0 = 0xfE;
	S12AD.ADCSR.BIT.ADST = 1;
	while (S12AD.ADCSR.BIT.ADST)
		;
	Front_SEN.off = FRONT_AD;
	RS_SEN45.off = RS45;
	LS_SEN45.off = LS45;
	RS_SEN2.off = RS2;
	LS_SEN2.off = LS2;
	getBattery();
}

void sensing_side2() {
	S12AD.ADANSA0.BIT.ANSA0 = 0x24;
	S12AD.ADCSR.BIT.ADST = 1;
	while (S12AD.ADCSR.BIT.ADST)
		;
	LS_SEN2.on = LS2;
	RS_SEN2.on = RS2;
}

void sensing_side() {
	S12AD.ADANSA0.BIT.ANSA0 = 0x12;
	S12AD.ADCSR.BIT.ADST = 1;
	while (S12AD.ADCSR.BIT.ADST)
		;
	LS_SEN45.on = LS45;
	RS_SEN45.on = RS45;
}

void sensing_front() {
	S12AD.ADANSA0.BIT.ANSA0 = 0x08;
	S12AD.ADCSR.BIT.ADST = 1;
	while (S12AD.ADCSR.BIT.ADST)
		;
	Front_SEN.on = FRONT_AD;
}


char startDecrease(char RorL) {
	if (RorL == R) {
		char flag = true;
		char flag2 = true;
		for (char i = 1; i < 3; i++) {
			if (sen_log_r[i] < sen_log_r[i + 1]) {
				flag = false;
			}
		}
		if (sen_log_r[0] < sen_log_r[1]) {
			flag2 = false;
		}
		return flag && !flag2;
	} else {
		char flag = true;
		char flag2 = true;
		for (char i = 1; i < 3; i++) {
			if (sen_log_l[i] < sen_log_l[i + 1]) {
				flag = false;
			}
		}
		if (sen_log_l[0] < sen_log_l[1]) {
			flag2 = false;
		}
		return flag && !flag2;
	}
	return false;
}

char isIncreaseFront(char RorL) {
	if (RorL == R) {
		char flag = true;
		for (char i = 0; i < 3; i++) {
			if (sen_log_front[i] < sen_log_front[i + 1]) {
				flag = false;
			}
		}
		return flag;
	} else {
		char flag = true;
		for (char i = 0; i < 3; i++) {
			if (sen_log_fl[i] < sen_log_fl[i + 1]) {
				flag = false;
			}
		}
		return flag;
	}
	return false;
}

#endif /* SENSOR_H_ */

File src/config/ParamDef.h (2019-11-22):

/*
 * ParamDef.h
 *
 *  Created on: 2013/11/21
 *      Author: Naoto
 */

#ifndef PARAMDEF_H_
#define PARAMDEF_H_

float TIRE = 24.745f;
float WHEEL;
float GEAR_A;
float GEAR_B;
float GEAR = 63.0 / 19.0;
float DUTY_MAX = 99.9f;
float Ke = 0.000368613538f;
float Km = 0.00352f;
float Resist = 2.93f;
float Mass = 0.106f;
float Lm = 0.001f;
float friction = 0.00125f;
float friction2 = 0.001925f;
float Tread = 0.074;

float running_wall_off_r = 500;
float running_wall_off_l = 500;

volatile float search_wall_off_r = 1500;
volatile float search_wall_off_l = 1400;

#define W_ENCORDER_LIMIT 100
#define W_ENCORDER_LIMIT2 10
#define W_ENCORDER_LIMIT_DIA 150
#define W_ENCORDER_LIMIT_DIA2 10
float gyroTh_R, gyroTh_L;
float pivotR, pivotL;
float Gkp, Gki, Gkd;
float Gkp2, Gki2, Gkd2;
float Akp, Aki, Akd;
float Akp2, Aki2, Akd2;
float Wkp, Wki, Wkd;
float Beta = 0;
float BetaOld = 0;
float k = 10;
float Vkp_r, Vki_r, Vkd_r;
float Vkp_l, Vki_l, Vkd_l;
float Vkp, Vki, Vkd;

#define orderup_r 4000
#define orderup_l 4000
#define supR_WALL 2000
#define supL_WALL 2000

float RF_WALL_EXIST2 = 800; //前壁補正　開始

//#define KIREME_R_DIA_SIDE 20
//#define KIREME_L_DIA_SIDE 20

/**
 * ↓　迷路・壁に依存する　調整パラメータ
 */

float wallhosei = 800;

/**
 * 調整以上
 */
int bias = 1;
int strBias = 3;
int diaBias = 3;
int Dia = 5;
int St1 = 7;
int minus = 4;
int Dia2;
int Dia3;
int St2;
int St3;

float R_WALL_OFF = 220;	//壁切れ　閾値
float L_WALL_OFF = 580;	//壁切れ　閾値
float R_WALL_OFF2 = 270;	//壁切れ　閾値
float L_WALL_OFF2 = 650;	//壁切れ　閾値
float R_WALL_OFF_D2 = 485;  //壁切れ　閾値　斜め用
float L_WALL_OFF_D2 = 740; //壁切れ　閾値　斜め用
float R_WALL_OFF_D = 570;  //壁切れ　閾値　斜め用
float L_WALL_OFF_D = 1000; //壁切れ　閾値　斜め用

float FRONT_WALL_ON = 610; //壁切れ　閾値　斜め用
float FRONT_WALL_ORDER = 420; //壁切れ　閾値　斜め用

float DIA_N_LEFT_WALL = 850; //壁切れ　閾値　斜め用
float DIA_N_RIGHT_WALL = 910; //壁切れ　閾値　斜め用

float DIA_FRONT_WALL_ORDER = 360; //壁切れ　閾値　斜め用

float existRightWall5 = 10000;  //壁切れの予備
float existLeftWall5 = 10000;   //壁切れの予備

float R_WALL_DIA = 1900;
float L_WALL_DIA = 1500;

float R_WALL_DIA2 = 1900;
float L_WALL_DIA2 = 1500;

float FRONT_CTRL_1 = 1275;   //前壁補正

void importFromDataFlash() {
	TIRE = *(float *) 1049216;
	myprintf("TIRE	%f	%d\r\n", TIRE, 1049216);
	GEAR_A = *(float *) 1049220;
	myprintf("GEAR_A	%f	%d\r\n", GEAR_A, 1049220);
	GEAR_B = *(float *) 1049224;
	myprintf("GEAR_B	%f	%d\r\n", GEAR_B, 1049224);
	DUTY_MAX = *(float *) 1049228;
	myprintf("DUTY_MAX	%f	%d\r\n", DUTY_MAX, 1049228);
	Ke = *(float *) 1049232;
	myprintf("Ke	%f	%d\r\n", Ke, 1049232);
	Km = *(float *) 1049236;
	myprintf("Km	%f	%d\r\n", Km, 1049236);
	Resist = *(float *) 1049240;
	myprintf("Resist	%f	%d\r\n", Resist, 1049240);
	Mass = *(float *) 1049244;
	myprintf("Mass	%f	%d\r\n", Mass, 1049244);
	Lm = *(float *) 1049248;
	myprintf("Lm	%f	%d\r\n", Lm, 1049248);
	friction = *(float *) 1049252;
	myprintf("friction	%f	%d\r\n", friction, 1049252);
	friction2 = *(float *) 1049256;
	myprintf("friction2	%f	%d\r\n", friction2, 1049256);
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

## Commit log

2018-02-11 cad data
    [MotorMount.DXF, QuantaAlter.DXF]
2018-02-12 parts list add
    [partslist.xlsx]
2018-02-28 初期設定追加
    [partslist.xlsx]
2018-04-16 1700対応
2018-08-06 抵抗値変更前
2018-09-04 東日本 バグ修正
